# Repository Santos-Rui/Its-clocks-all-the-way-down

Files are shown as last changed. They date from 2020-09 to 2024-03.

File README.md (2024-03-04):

## Its clocks all the way down...

A digital clock made of 24 analog clocks.

Powered by an arduino, each clock handle is a stepper motor, totaling 48 steppers.

Why? because i'm part time masochist and like having to do the same thing dozens of times 

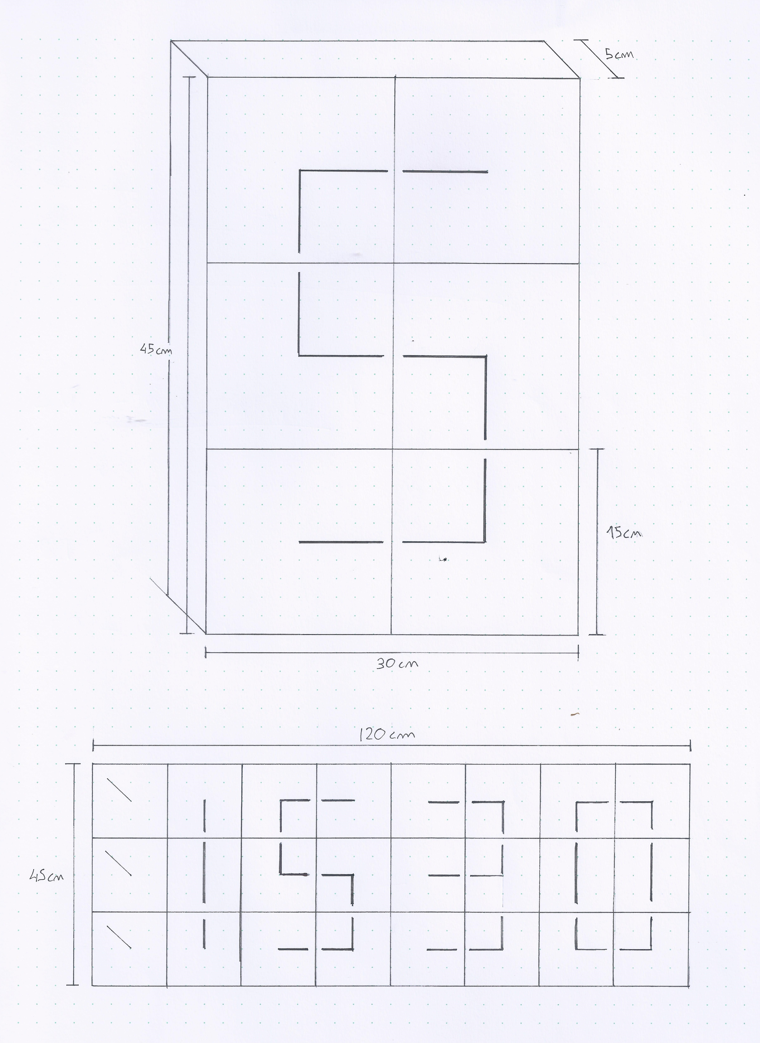
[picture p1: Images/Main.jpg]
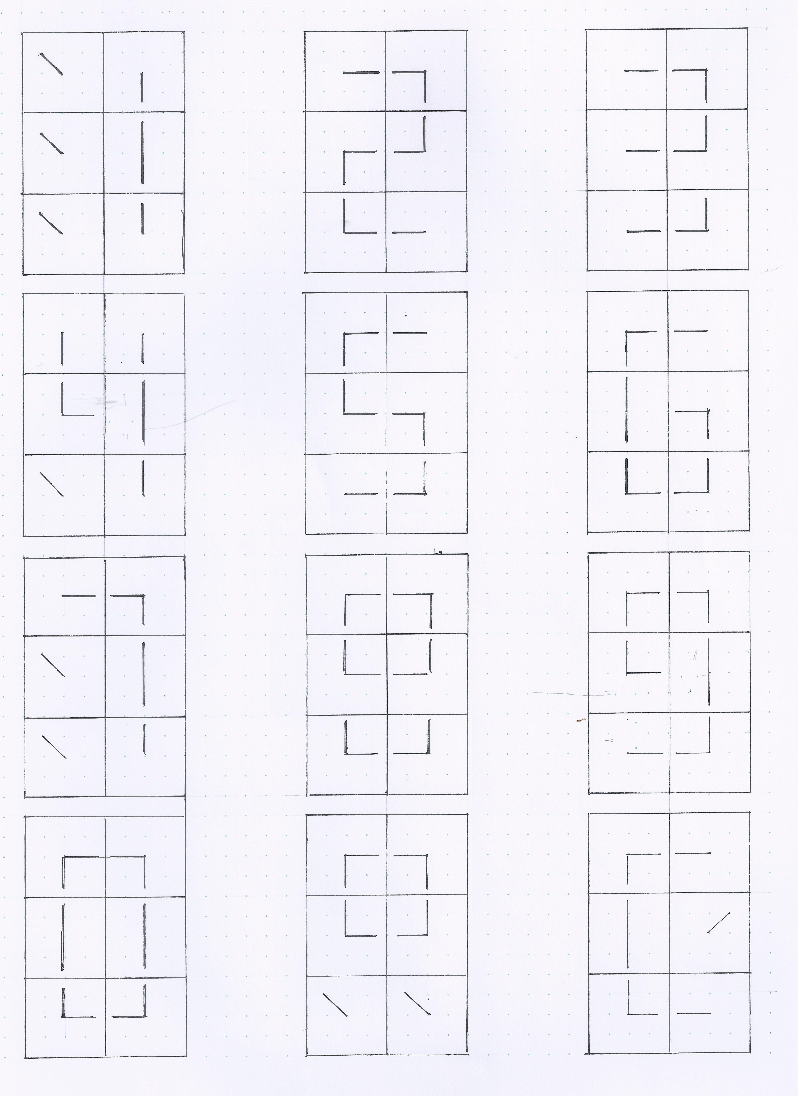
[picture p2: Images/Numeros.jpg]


[Click here for Video](https://www.youtube.com/watch?v=mT9d-I6LFRw)

~~The clock body, gears and handles will be laser cut (3 or 5mm) MDF, the handle shafts (shaft?) will be made with solid 8mm and 10mm alu with 1mm wall. All pieces (but the gears) will be designed from scratch in corel draw.~~

The clock "main body" will probably still be plywood/mdf. The body will now be only a front plate where the clock modules, psu, arduino and cables will atach (Maybe a back one for structure/tidiness). Later i can just do a thin pretty front cover and hide the screws. I will have to drill by hand though, the full clock wont fit the laser cutter.

The clock mechanism modules will now be fully 3d modeled printed, contaning ball bearings. Super gluing mdf to alu was already hard, keeping it all straight and square proved almost impossible and the end result was way too fragile. Modularity will allow me to swap/fix any clock without having to disassemble the whole thing. This will also probably help reducing slack and noise while increasing smootheness in the rotation

I'll also develop all the code (using some stepper libs) which will probably include some animations to make the transitions look nice, some kind of remote control, and maybe a small display for UI.

Also if you are still reading this, please help me design a better number 8.

## Version 1 
A simple, scaled down version using off the shelf gears. Only 1 clock for proof of concept
<details>
  <summary>Click to see more!</summary>
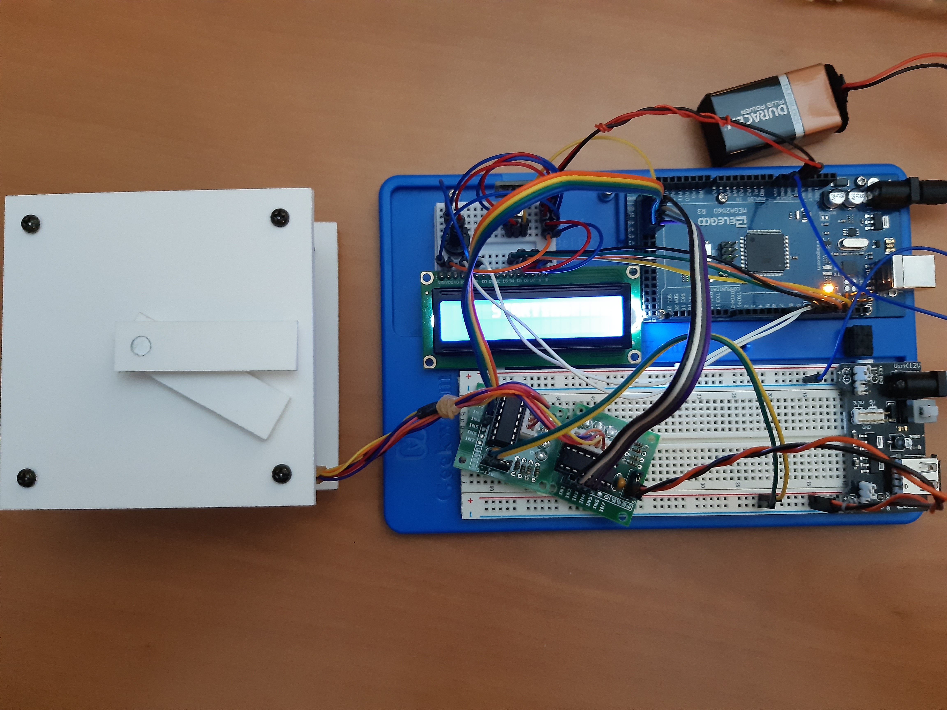
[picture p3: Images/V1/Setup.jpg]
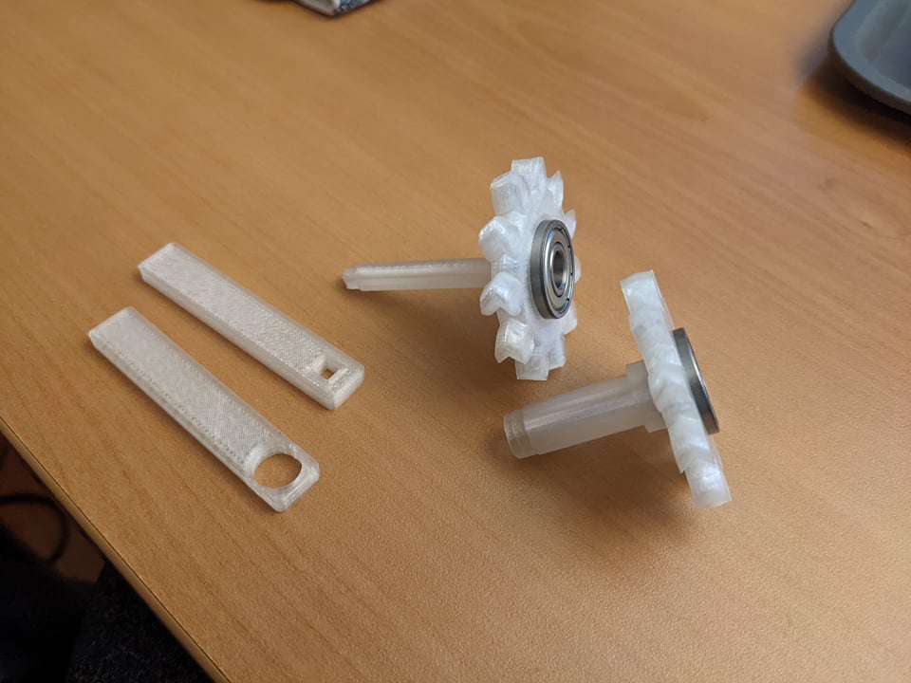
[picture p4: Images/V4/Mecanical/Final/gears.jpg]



</details>

## Version 2 
A full sized number (6 clocks, 12 motors). This will  already house the full size final power supply and the plan is to make it modular, so i can just add 3 more in the V3. Here ill need to implement some prettier control for the motors to move them in sync, and maybe some prettier transitions.
<details>
  <summary>Click to see more!</summary>

Fit test



Diagrams to laser cut

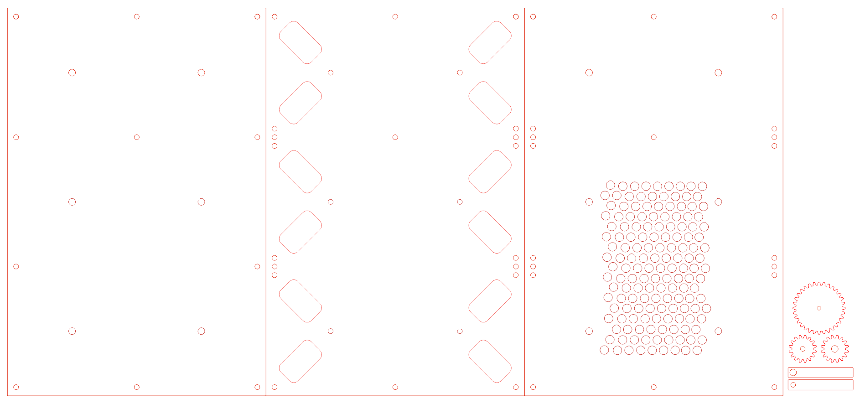
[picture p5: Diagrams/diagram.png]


First laser cutting try

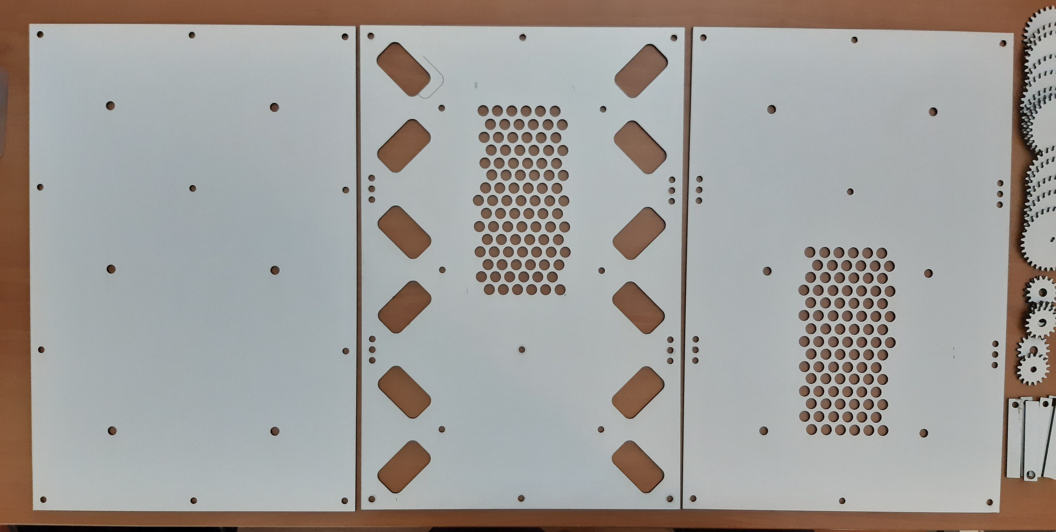
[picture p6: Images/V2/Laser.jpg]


Motors and corresponding gears installed. Also power supply and some power cable routing

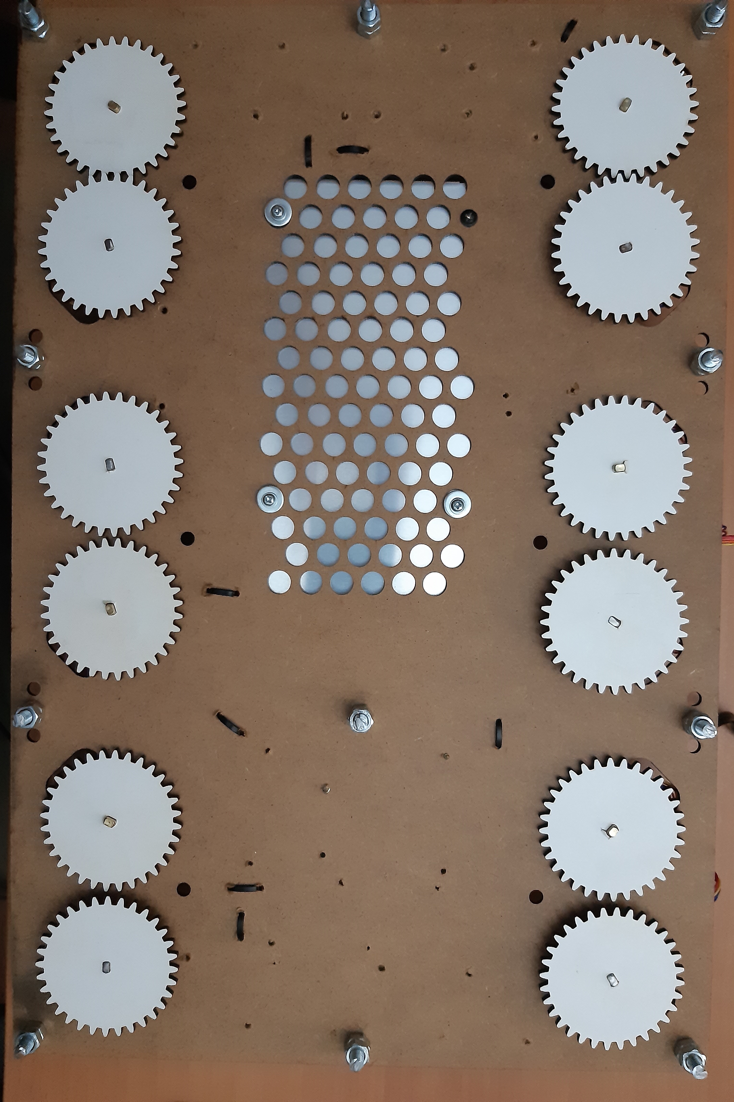
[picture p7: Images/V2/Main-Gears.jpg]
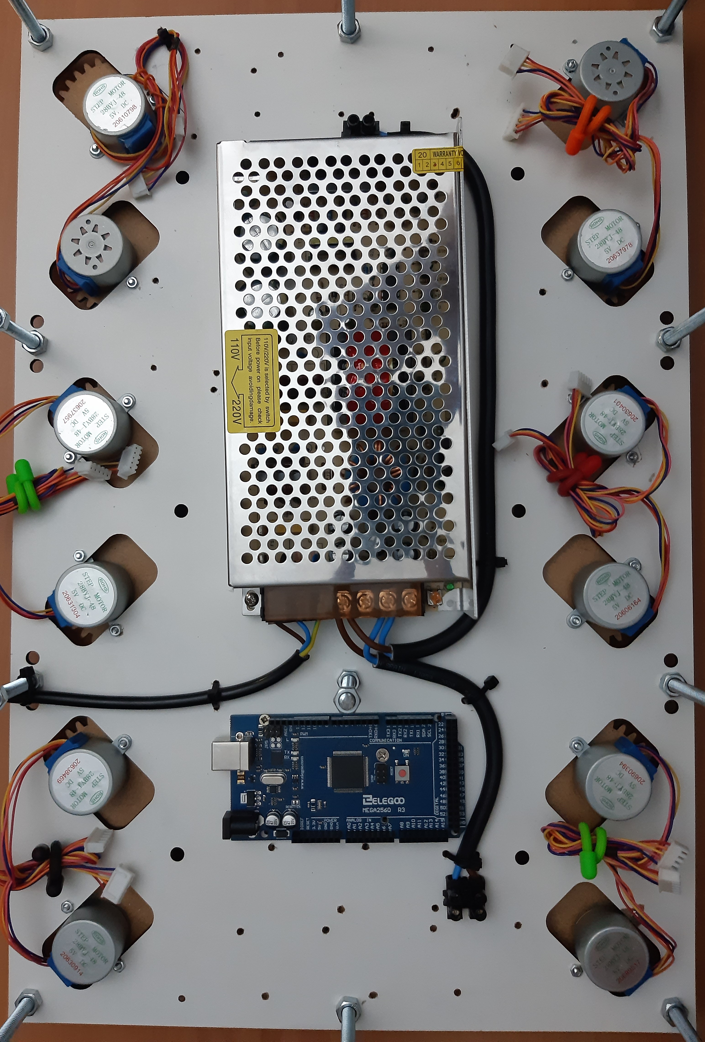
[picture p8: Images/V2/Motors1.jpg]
 

All driver boards installed, and motor cables routed.

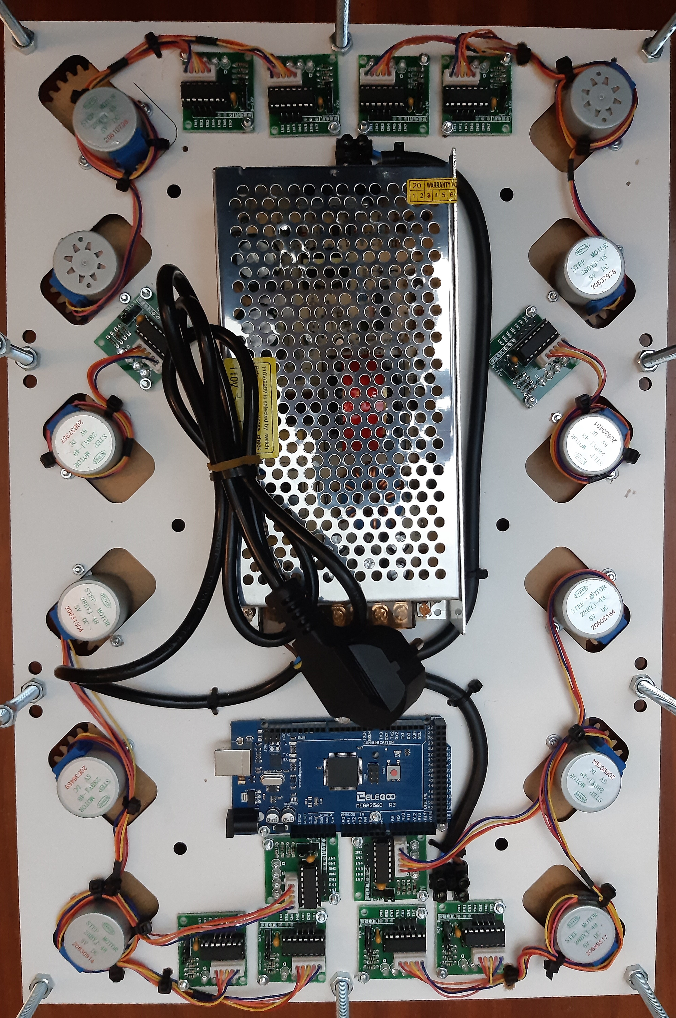
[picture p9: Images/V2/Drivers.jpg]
 

The plan was to solder every power and data cable, but soldering iron is shit and makes it way too hard, while the new one doesnt come, ill settle for custom cable lenght. Seems tidy enough

All power cables done

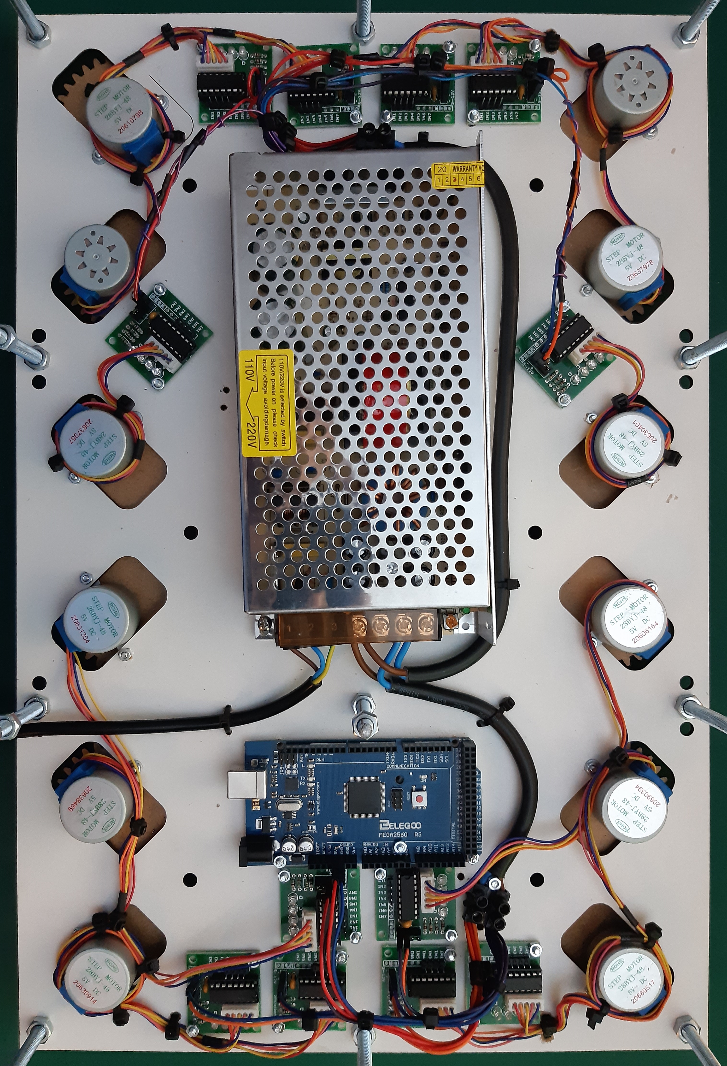
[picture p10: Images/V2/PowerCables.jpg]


At this point the soldering iron tip commited sudoku and melted itself, somehow. So for now ill have this spaghetti bundle of data cables to match the code i'll write for it after. After fixing a bunch of faulty cables, everything seems to be working on both eletrical and mechanical side.

 

The only problem is related to the gears. At this point the clock handles have somewhere between 5 and 10 degrees of play, not even close to acceptable. I ended up drilling the mottor mounts by hand, which led to some clearance between the cogs, added to the 2:1 ratio that doubled the ammount of error. I will need another iteration before going for the full clock only to handle the mechanical part.

### Coding

At this point i can start with the coding. The obvious problem is that moving a motor is a blocking function, so to move many motors simultaneously i will need to move all of them in tiny increments at a very fast pace. The AccelStepper library handles this already(to a degree), but i'm going to try an implementation from scracth. Ill compare it against AccelStepper later and see which fits better.
</details>

## Version 3 
A second iteraion with only number display, the backlash in the gearing was way to high, making it unusable.

<details>
  <summary>Click to see more!</summary>
The code was kinda working, but i need better base to actually test it. Ill redo V2 with a new mid-plate, and try to sodder everything, instead of connecting. 

Made some mockups to test the tolerance. Computer modeling can only take me so far, the laser cut, even though only 0.2mm ends up adding up to a big error

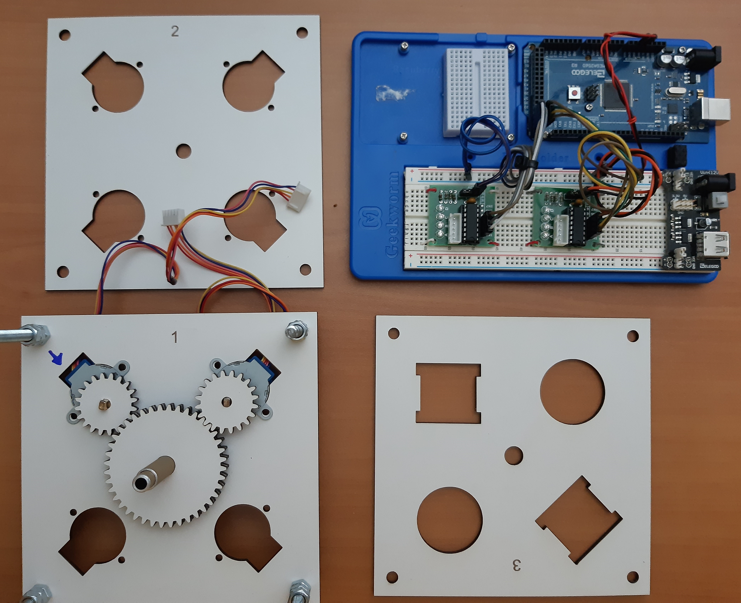
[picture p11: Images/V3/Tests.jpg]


And a new midplate is born

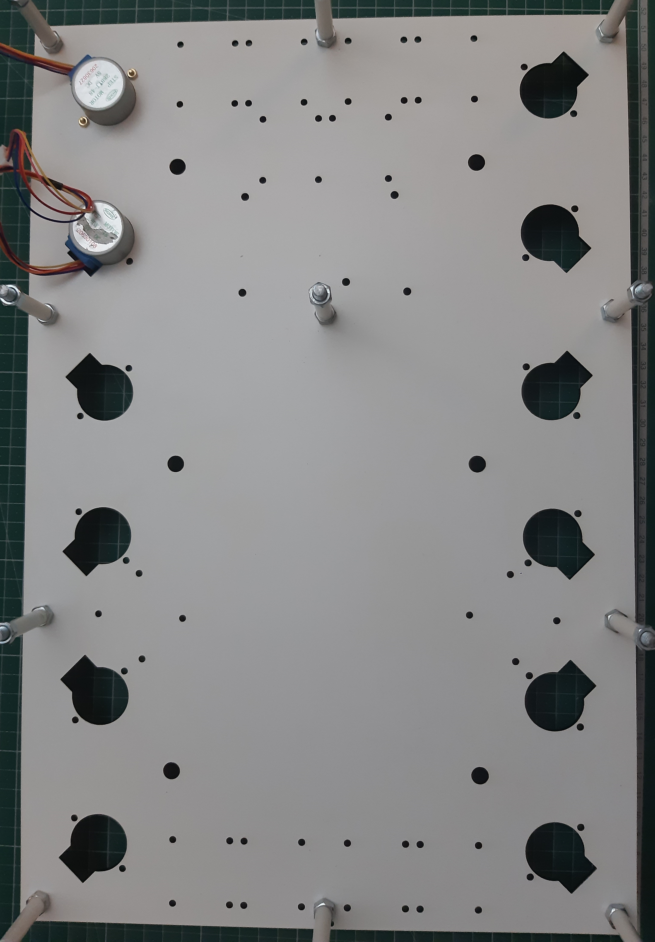
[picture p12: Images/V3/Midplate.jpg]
 

I could make it cleaner, but its good enough

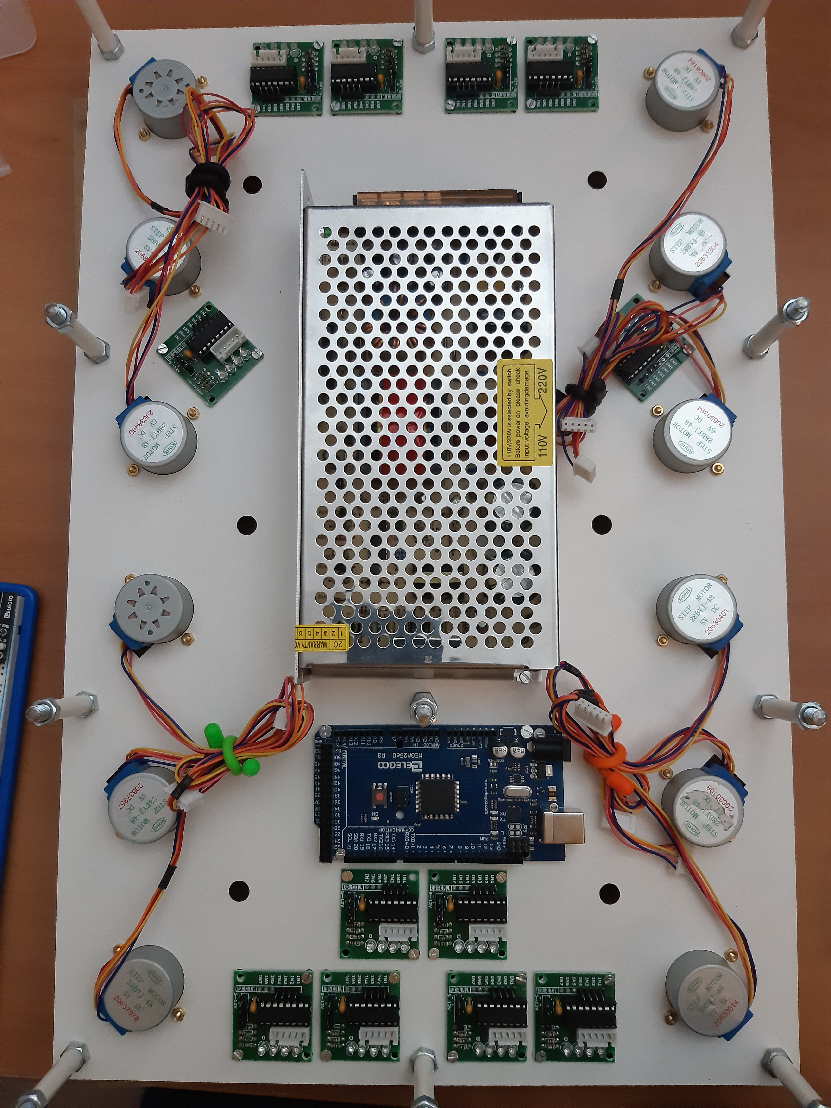
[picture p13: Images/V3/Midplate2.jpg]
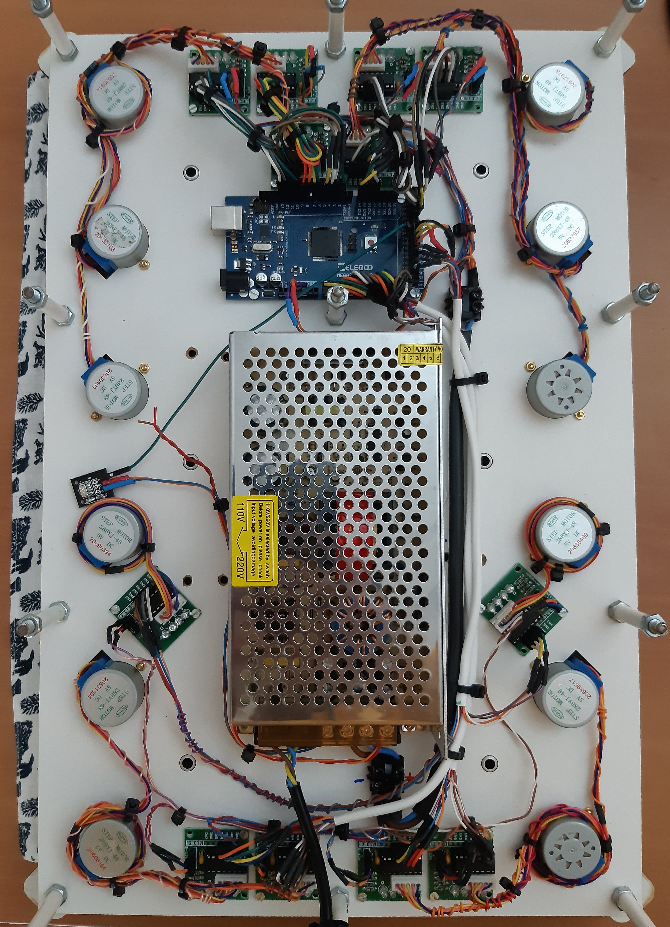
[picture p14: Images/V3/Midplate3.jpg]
 

On the mechanical side of things, gears are now running way smoother and with a fraction on the backlash.



A bit of code and some clock dials and we got
[Click here for Video](https://www.youtube.com/watch?v=mT9d-I6LFRw)
V3 Video (https://www.youtube.com/watch?v=mT9d-I6LFRw "V3 Video")

Im pretty happy with the results, not sure ill go any further, the repetitiveness  of the project is a bit overwhelming

</details>

## Version 4 
(Current) has 2 major differences. Modular clock mechanisms, 3d modedeled and printed. On the eletronics side i will need to expand the IO using shif registers or anything else that works really; the previous iteration had every stepper connected directly, which works but limits me at aprox 15 steppers.

<details>
  <summary>Click to see more!</summary>
  
  Prototyping
  
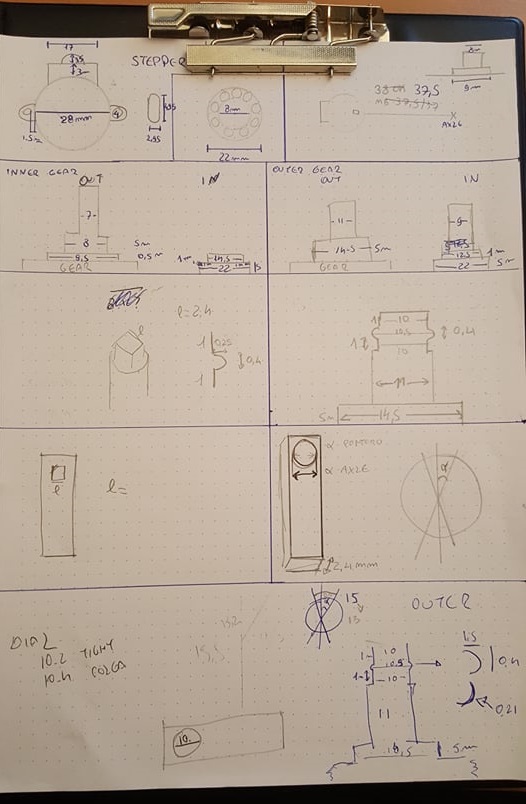
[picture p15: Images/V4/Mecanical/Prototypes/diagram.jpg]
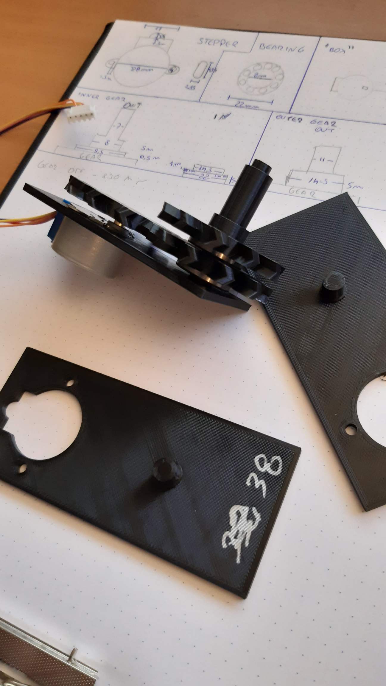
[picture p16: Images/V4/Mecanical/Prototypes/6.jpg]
     
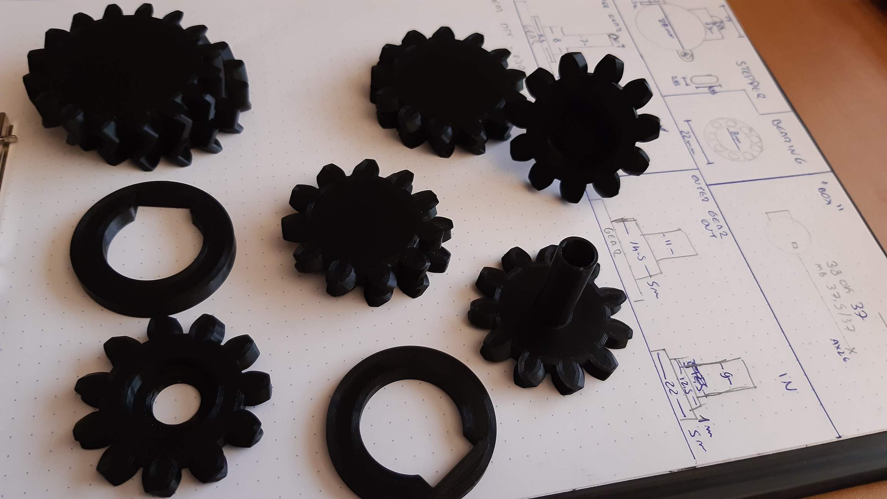
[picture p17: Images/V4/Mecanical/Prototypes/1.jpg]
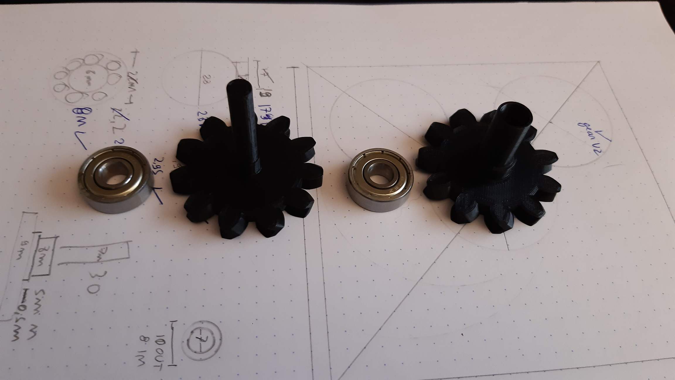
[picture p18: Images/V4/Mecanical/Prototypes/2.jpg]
            
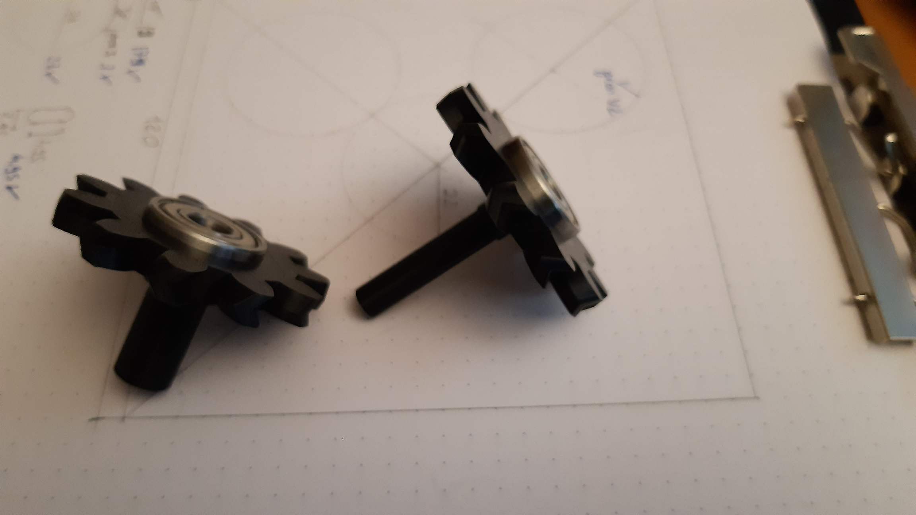
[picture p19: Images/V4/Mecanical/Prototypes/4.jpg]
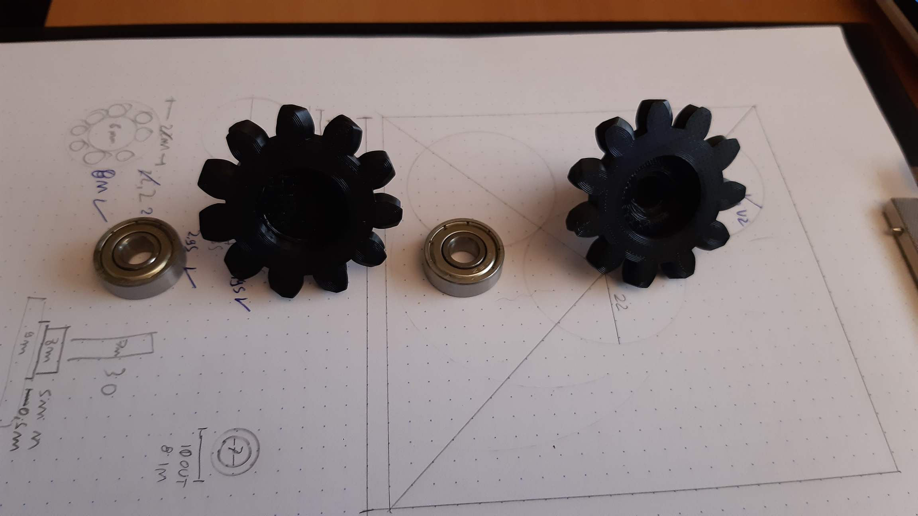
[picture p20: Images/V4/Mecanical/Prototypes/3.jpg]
      
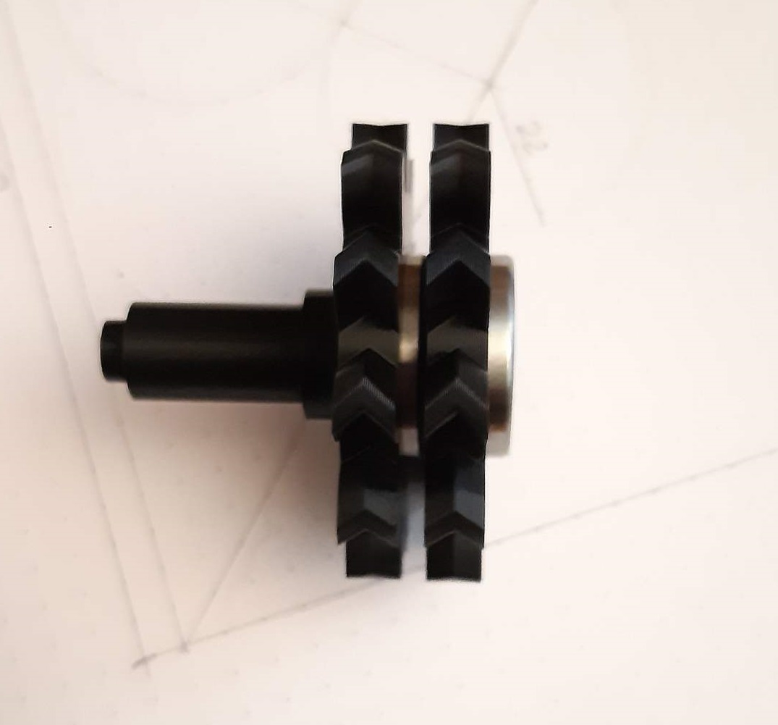
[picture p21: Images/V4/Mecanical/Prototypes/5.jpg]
  

  And the final mechanical version

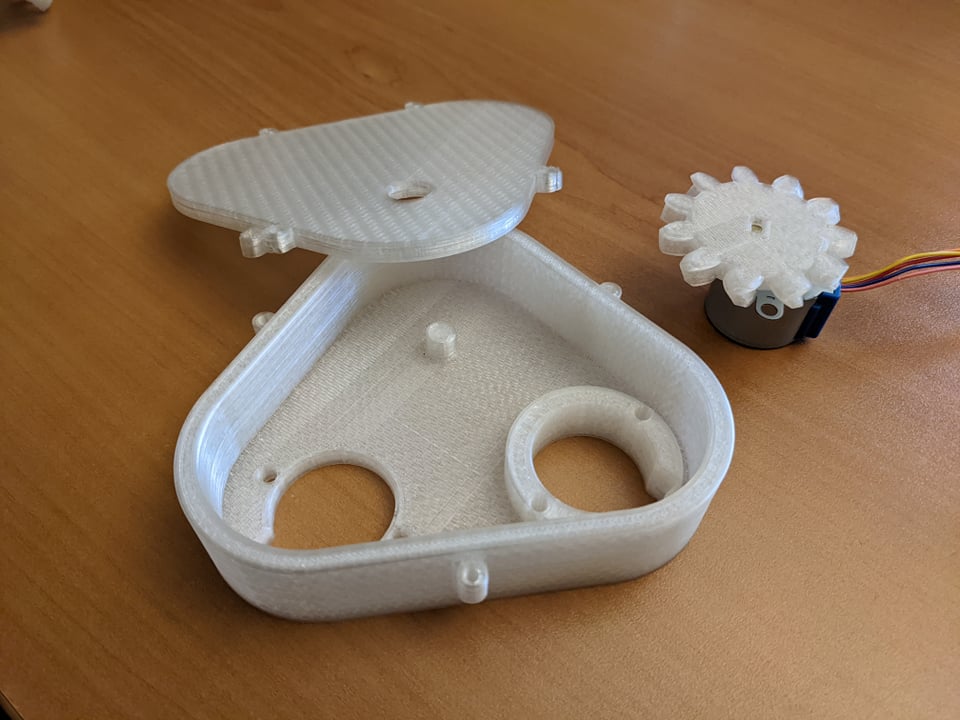
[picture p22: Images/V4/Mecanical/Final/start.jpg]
      
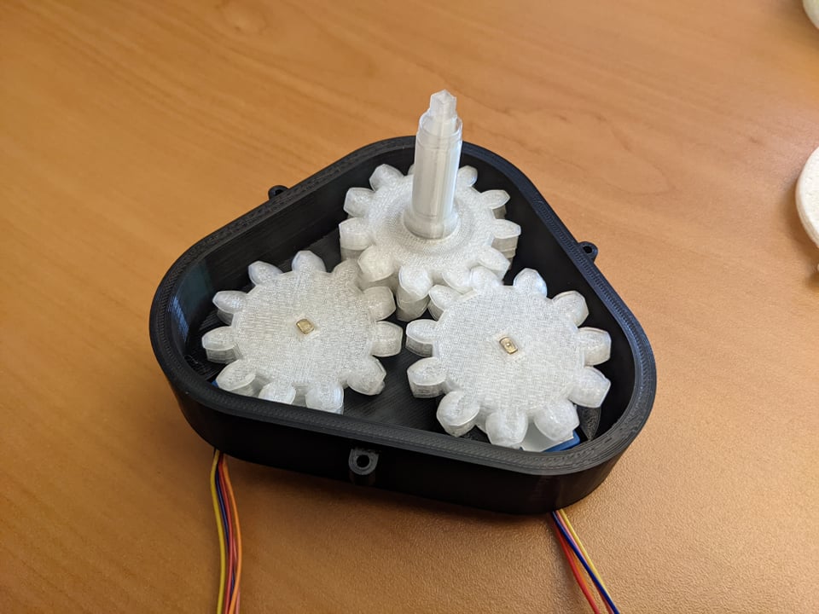
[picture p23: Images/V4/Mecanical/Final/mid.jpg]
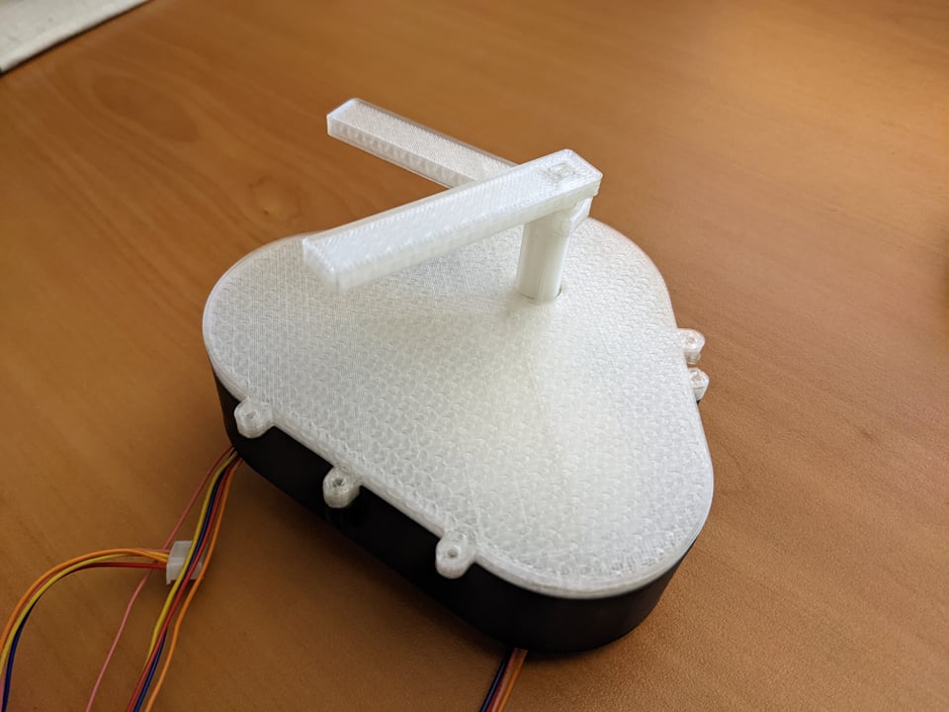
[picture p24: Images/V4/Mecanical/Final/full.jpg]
      

  The "final" version had some problems with slack. When using a bottom bearing to support both gears, meant the top one would have the combined play of both bearings. So i designed a finalfinal version, with a third bearing on top that couples to the lid, this way the gear assembly has almost zero lateral play.
  
     
          
     

  For the eletrical side of things, i pretty much given up on shift registers, so i'll most likely end up using one arduin for every digit, so 4 for the full clock.
  Comunication betwen arduinos seems easy, i might end up using a fifth arduino (a uno maybe) to calculate the positions of every dial, send them to the slaves and sync the start of movement.
  
  Since This time the plan is to actually build a clock and not a "digit", ill start by building the base board that will hold everything together. A 120x45cm board. Something like this
  
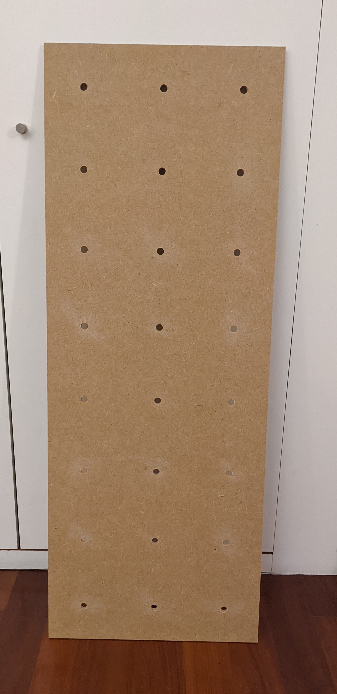
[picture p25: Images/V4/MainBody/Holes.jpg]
     
  
  Add a psu and some power cables
  
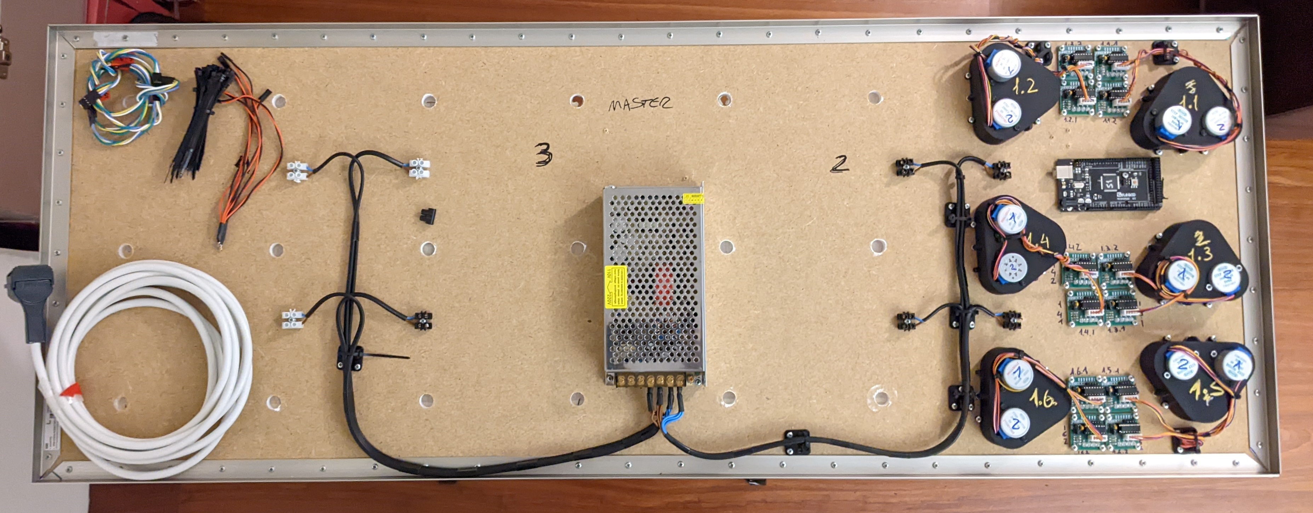
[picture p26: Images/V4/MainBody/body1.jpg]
     
  
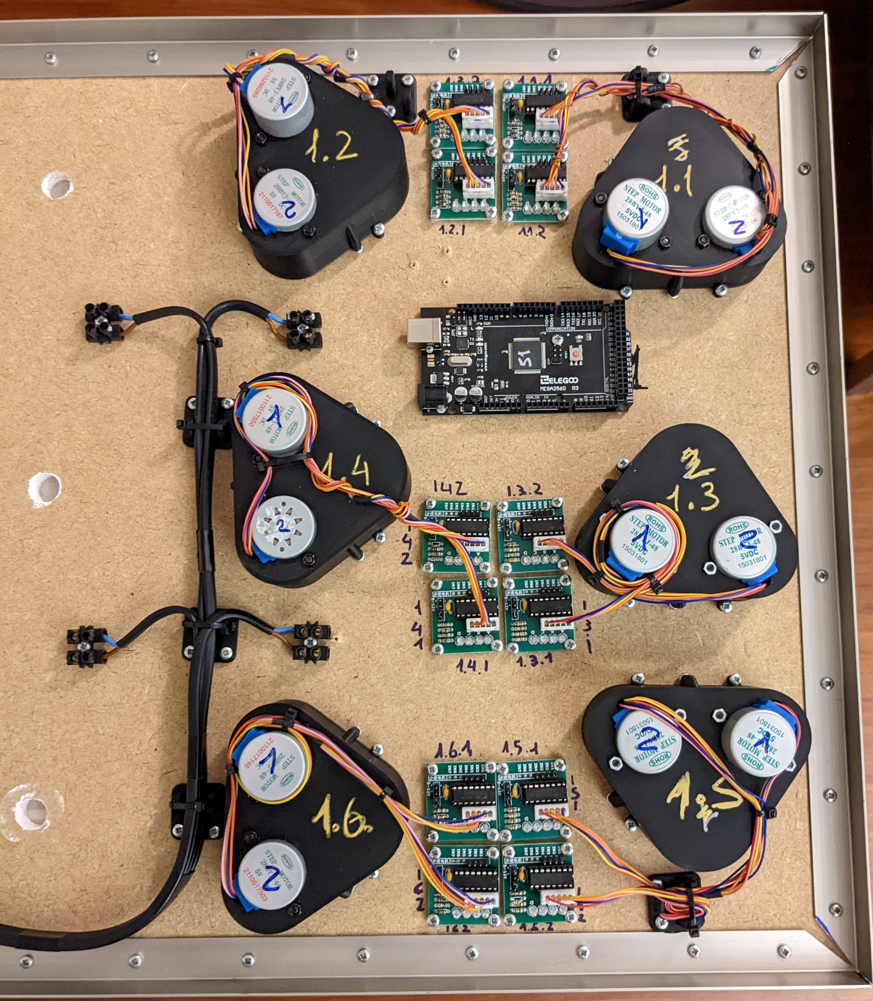
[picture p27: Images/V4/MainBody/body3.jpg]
  

  Some more data cables, and we have a functioning master slave/configuration. The slave is agnostic of any logic or numbers, it only receives positions, and some configs on how to move. After sending all the data, an aditional signal is sent to start moving every slave at once.
    
  
</details>

## Version N+1
This would be making it double, or 4 times as big so i could play with the animations and different number designs. Most likely will never exist.

## TO DO
<details>
  <summary>Click to expand!</summary>
  
Shift Registers - Expand IO - Nope

Using the same cable for 1-2 pin on every motor can theoretically give me 50% less IO ports needed. This will most likely NOT work - Nope

Turning every motor on and off on every step can also theoretically make me only need the current that one motor uses, and make it possible to wire them all in the same  circuit only using like 500mA , but can lead to drift overtime, will need testing. - Probably nope
</details>

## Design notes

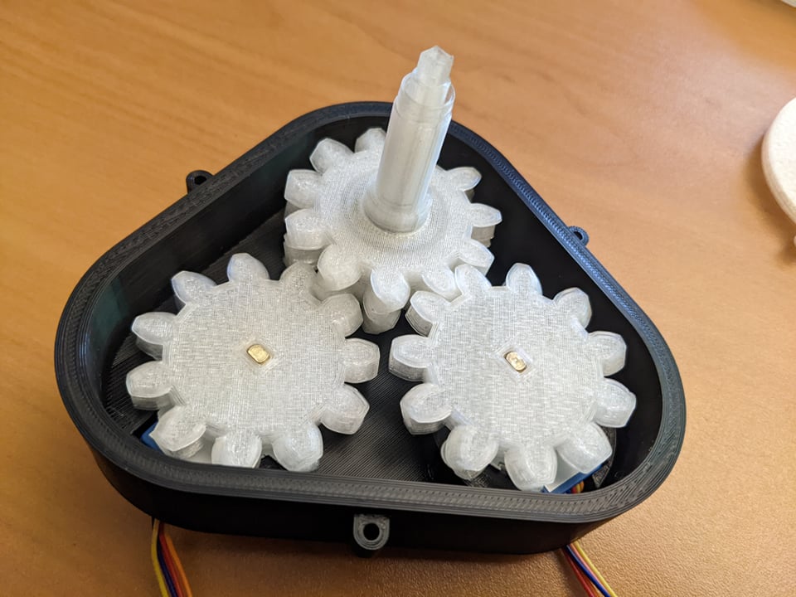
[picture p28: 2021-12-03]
Images/V4/Mecanical/Final/mid2.jpg

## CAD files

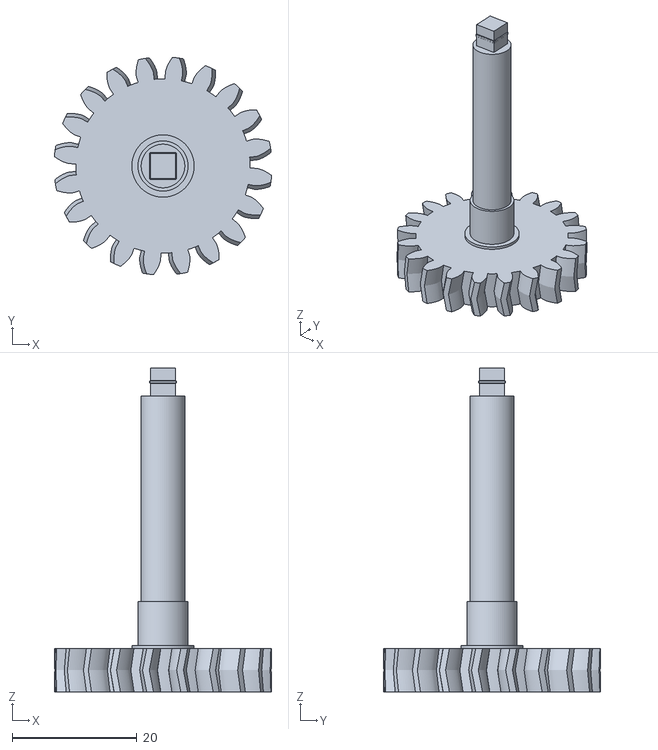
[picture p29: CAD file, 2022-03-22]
STL's/V2 Inner Gear v13.stl
34.9 x 34.9 x 52.0

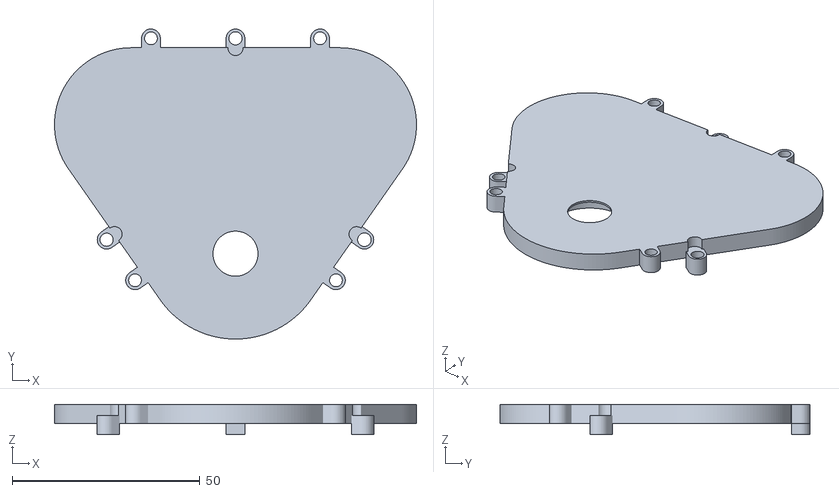
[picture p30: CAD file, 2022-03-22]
STL's/Cover.stl
96.5 x 82.6 x 8.00

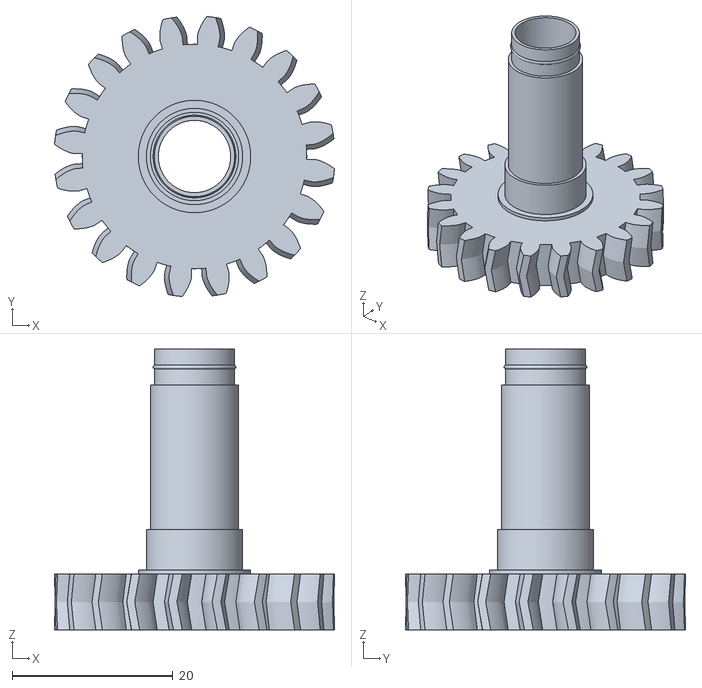
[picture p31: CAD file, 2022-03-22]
STL's/V2 Outer Gear v10.stl
34.9 x 34.9 x 35.0

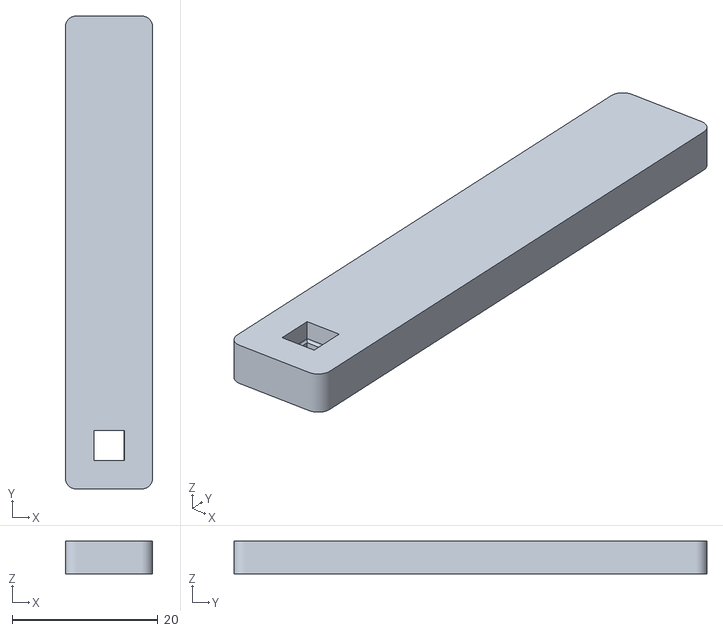
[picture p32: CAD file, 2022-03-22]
STL's/Dial in v4.stl
12.0 x 65.0 x 4.50

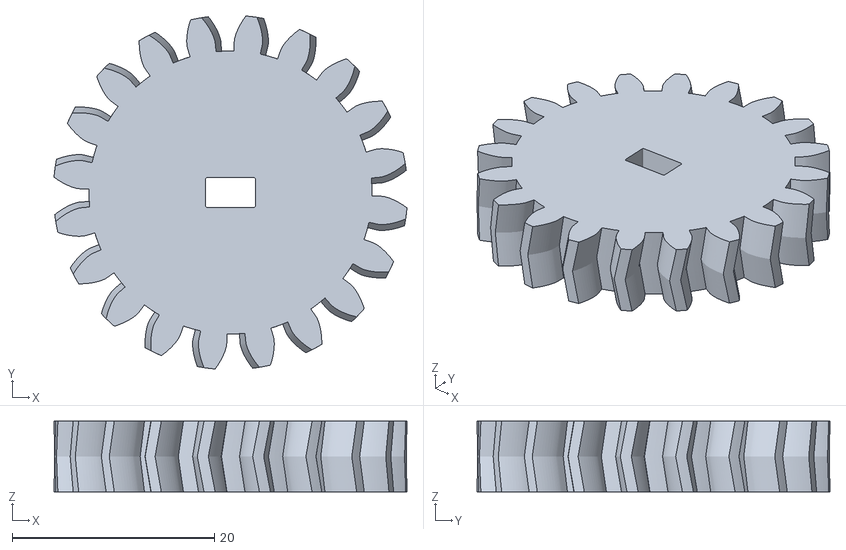
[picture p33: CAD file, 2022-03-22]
STL's/V2 Stepper Gear v9.stl
34.9 x 34.9 x 7.00

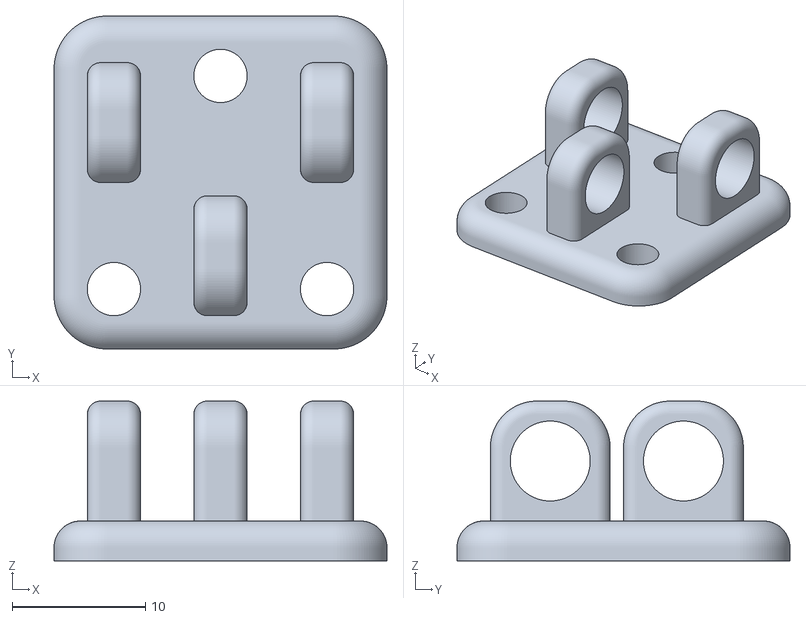
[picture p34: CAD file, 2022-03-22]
STL's/Cable tie clock v1.stl
25.0 x 25.0 x 12.0

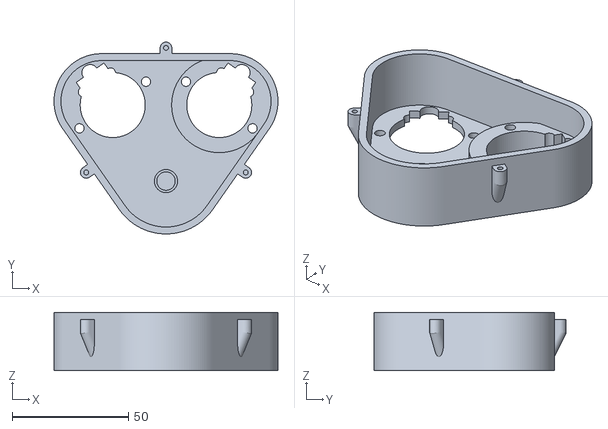
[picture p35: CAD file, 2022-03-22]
STL's/box.stl
96.5 x 82.6 x 25.0

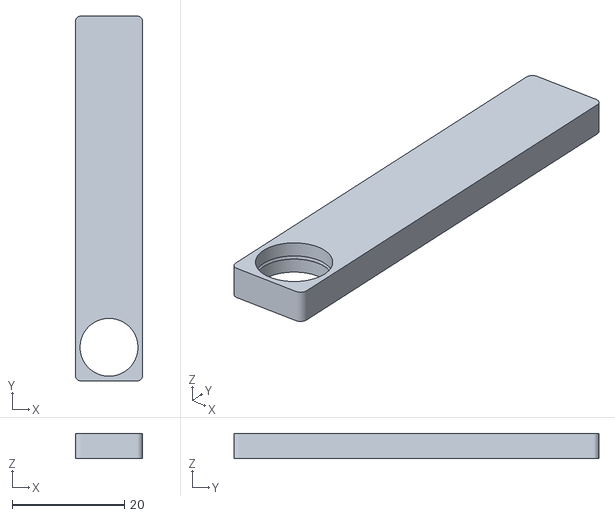
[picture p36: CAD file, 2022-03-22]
STL's/Dial out v2.stl
12.0 x 65.0 x 4.50

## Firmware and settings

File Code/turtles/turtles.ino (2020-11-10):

//  code for the V3 clock

#include <Stepper.h>
#include <IRremote.h>


const int stepsPerRev = 2048; // change this to fit the number of steps per revolution
const int lapFull = 4096;
const int qlap = 1024;

const int RPM = 15;           // Adjustable range of 28BYJ-48 stepper is 0~17 rpm
const int nrMotors = 12;

// IR
int RECV_PIN = 34;
IRrecv irrecv(RECV_PIN);
decode_results results;
unsigned long key_value = 0;
//IR

int rest[12]={0,0,0,0,0,0,0,0,0,0,0,0};
int zero[12]={1024,2048,2048,3072,0,2048,0,2048,0,1024,0,3072};
int um[12]={3584,3584,2048,2048,3584,3584,0,2048,3584,3584,0,0};
int dois[12] = {1024,1024,3072,2048,1024,2048,0,3072,0,1024,3072,3072};
int tres[12] ={1024,1024,3072,2048,1024,1024,3072,0,1024,1024,3072,0};
int quatro[12] ={2048,2048,2048,2048,0,1024,0,2048,3584,3584,0,0};
int cinco[12] ={1024,2048,3072,3072,0,1024,2048,3072,1024,1024,0,3072};
int seis[12] ={1024,2048,3072,3072,0,2048,2048,3072,0,1024,3072,0};
int sete[12] ={1024,1024,3072,2048,3584,3584,2048,0,3584,3584,0,0};
int oito[12] ={1024,2048,2048,3072,0,1024,0,3072,0,1024,0,3072};
int nove[12] ={1024,2048,2048,3072,0,1024,0,2048,1024,1024,0,3072};


typedef struct smotor {
  int currentPos = 0;
  int targetPos = 0;
  int lap = 0;
  int pins[4];
  Stepper * stepper;

  smotor(int a, int b, int c, int d){
      stepper = new Stepper(stepsPerRev, a , c , b , d);
      pins[0]=a;pins[1]=b;pins[2]=c;pins[3]=d;
      currentPos=targetPos=lap=0;
  }

  void setTarget(int target) {
      if(target<=currentPos){lap=1;}  //se tivermos a fretne temos de dar a volta
      
      targetPos = target;

  }

  void step() {

      if (currentPos==lapFull){
          currentPos=0;
          lap--;
      }
      if (lap > 0 || currentPos < targetPos){
          stepper->step(1);
          currentPos++;
      } 
//      Serial.println("Exiting step  lap =");
//      Serial.println(lap);
//      Serial.println("Cpos =");
//      Serial.println(currentPos);
//      Serial.println("Tpos =");
//      Serial.println(targetPos);
  }
}*motor;

//1 2 
//3 4
//5 6
motor listaMotors[nrMotors];

void createMotor() {
  listaMotors[0] = new struct smotor( 14  , 15 ,  16, 17 );  //1 top       
  listaMotors[1] = new struct smotor( 22 ,  24  ,26 , 28 );  //1 bottom   
  
  listaMotors[2] = new struct smotor( 2  ,  3  , 4  ,  5 );  //2 top         
  listaMotors[3] = new struct smotor( 6 ,   7  ,  8 ,  9 );  //2 bottom     
  
  listaMotors[4] = new struct smotor( 23 ,  25 , 27 , 29 );  //3 top       
  listaMotors[5] = new struct smotor( 38 ,  40  ,42 , 44 );  //3 bottom
  
  listaMotors[6] = new struct smotor( 10 ,  11 , 12 , 13 );  //4 top           
  listaMotors[7] = new struct smotor( 46 , 48  , 50 , 52 );  //4 bottom  
  
  listaMotors[8] = new struct smotor( A0,  A1 ,  A2,  A3 );  //5 top    
  listaMotors[9] = new struct smotor( A4,  A5 ,  A6 , A7 );  //5 bottom 
  
  listaMotors[10] = new struct smotor( A8,  A9 , A10, A11 );  //6 top        
  listaMotors[11] = new struct smotor( A12,  A13, A14, A15);  //6 bottom     
}


void motorSetup() {
  for (int i = 0; i < nrMotors; i++) {
    listaMotors[i]->stepper->setSpeed(RPM);
  }
}


void turnOffAll(){
  for (int i = 0; i < nrMotors; i++) {
        digitalWrite(listaMotors[i]->pins[0], LOW);
        digitalWrite(listaMotors[i]->pins[1], LOW);
        digitalWrite(listaMotors[i]->pins[2], LOW);
        digitalWrite(listaMotors[i]->pins[3], LOW);
    }
}


void moveAll(){


    for (int i = 0; i < nrMotors; i++) {
        listaMotors[i]->step();
    }
}

void draw(int lista[12]){
  for(int a=0;a<12;a++){
    listaMotors[a]->setTarget(lista[a]);
  }
}

void setup(){
    Serial.begin(9600);

    createMotor();
    motorSetup();
    irrecv.enableIRIn(); // Start  receiver

    delay(2000);
    Serial.println("exiting setup");
}


void loop() {
  if (irrecv.decode(&results)) {
  // if (results.value == 0XFFFFFFFF){
  //   results.value = key_value;
  // }

    switch(results.value){
        
      case 0xFF30CF:    // 1  
      case 0x9716BE3F: 
          draw(um); 
      break;

      case 0xFF18E7:   // 2
      case 0x3D9AE3F7:
          draw(dois); 
      break;

      case 0xFF7A85:   // 3
      case 0x6182021B:
          draw(tres); 
      break;

      case 0xFF10EF:   // 4
      case 0x8C22657B:
          draw(quatro); 
      break;

      case 0xFF38C7:   // 5
      case 0x488F3CBB:
        draw(cinco); 
      break;

      case 0xFF5AA5:   // 6
      case 0x449E79F:
         draw(seis); 
      break;

      case 0xFF42BD:   // 7
          draw(sete);
      break;

      case 0xFF4AB5:   // 8
      case 0xFF1BC01:
          draw(oito);
      break;

      case 0xFF52AD:   // 9
          draw(nove);
      break;

      case 0xFF6897:   // 0
          draw(zero);
      break;



      case 0xFFA25D:   // POWER
          draw(rest);
      break;


      default:
      break;
        }



       
      //Serial.println(results.value, HEX);
      key_value = results.value;
      irrecv.resume();// Receive the next value
  }

  moveAll();
  //delay(30000);
}

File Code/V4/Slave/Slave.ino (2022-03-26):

#include <Dto.h>
#include <CustomStepper.h>  
#include <Stepper.h>
#include <Wire.h>                               

//number of the slave
const int slaveNr = 1; //hours number 1 (left)

//pin to trigger movement
int triggerPin = 25;    

// RGB Pins
#define BLUE 29
#define GREEN 31
#define RED 33


//stepper settings
const int stepsPerRev = 2048; //steps per revolution
const int RPM = 15;           // Adjustable range of 28BYJ-48 stepper is 0~17 rpm
const int nrOfSteppers = 12;


//control vars
boolean listeningMode = true;
boolean waitingMode = true;
static int steppersDone = 0;


//"buffers"
int val = 0;      // variable to store the read value
String buffer = "";


//Stepper positions
int stepPos[nrOfSteppers][4] = {
      {22,24,26,28},  {2 ,3, 4 ,5 }       ,    {10,11,12,13} ,  {6, 7, 8, 9},     // 1.1-1.2      2.1-2.2      1 2 
      {A4,A5,A6,A7},{A12,A13,A14,A15}     ,    {A0,A1,A2,A3} , {A8,A9,A10,A11},   // 3.1-3.2      4.1-4.2      3 4
      {47,49,51,53} , {39,41,43,45}       ,    {38,40,42,44} ,  {46,48,50,52}     // 5.1-5.2      6.1-6.2      5 6
};


//main struct
CustomStepper * stepperList[nrOfSteppers];


//intializes steppers with pins and rpm
void intializeMotors() {
    for (int i = 0; i < nrOfSteppers; i++) {
        stepperList[i] = new CustomStepper(stepsPerRev,stepPos[i][0],stepPos[i][1],stepPos[i][2],stepPos[i][3]);
        stepperList[i]->setRPM(RPM);
    }   
}


//maps the received dto to the global struct
void mapDtoToStruct (Dto dto) {
    for (int i = 0; i < nrOfSteppers; i++) {
        stepperList[i]->setTarget(dto.getData(i), dto.getLap(), dto.getShortest(), dto.getDirection());
    }
  }


//handles i2c recevive event
//reads byte by byte and writes it to a string untill the last char '}'
void receiveEvent(int size){
    Serial.println("\nreceved event");
    int i=0;
    while(0<Wire.available()){    
        char c = Wire.read();
        if (c == '!'){
          waitingMode = false;
          return;
          }
        
        buffer = buffer + c;
        if(c=='}'){
            Serial.println("Full string");
            Serial.println(buffer);
            listeningMode = false;
            break;
        }
    }
}


void setup(){
    Serial.begin(9600);
    Serial.println("Starting Setup");
    pinMode(RED, OUTPUT); pinMode(GREEN, OUTPUT); pinMode(BLUE, OUTPUT);
    digitalWrite(RED, HIGH);digitalWrite(GREEN, HIGH);digitalWrite(BLUE, HIGH); //white
    //Join i2c as a slave                           
    Wire.begin(slaveNr);
            
    //register the receiver                        
    Wire.onReceive(receiveEvent);

    //Steppers
    intializeMotors();
    delay(3000);
    digitalWrite(RED, LOW);digitalWrite(GREEN, LOW);digitalWrite(BLUE, LOW); //OFF
    Serial.println("Exiting setup");
    
}


void loop() {
    Serial.println("Starting loop Iteration...");    
    Serial.println("Starting waiting for data...");
    digitalWrite(RED, LOW);digitalWrite(GREEN, LOW);digitalWrite(BLUE, HIGH); //BLUE
    while (listeningMode){
        delay(25);
    }
    digitalWrite(RED, HIGH);digitalWrite(GREEN, LOW);digitalWrite(BLUE, LOW); //red
    
    Serial.println("Received data, creating dto...");
    Dto dto;
    dto.setDto(buffer);
    
    Serial.println("Mapping dto...");
    mapDtoToStruct(dto);

    //Clear buffer
    buffer = "";

    //Wait for the trigger to actually start moving
      Serial.println("Starting waiting for trigger wire...");
      while(waitingMode) {
  //      val = digitalRead(triggerPin); // read the input pin
  //      Serial.print("val = "); Serial.println(val);
  //      if (val == HIGH) {
  //            int highs = 0;
  //            while (highs<100) {
  //                val = digitalRead(triggerPin); // read the input pin
  //                if (val == HIGH) {
  //                    highs++;
  //                }
  //                else {break;}
  //            }
  //            if(highs == 100){
  //                waitingMode = false;
  //            }
//
  //      }
        delay(20);
    }
    digitalWrite(RED, HIGH);digitalWrite(GREEN, LOW);digitalWrite(BLUE, HIGH); //purple
    //move untill every stepper is done
    Serial.println("Moving...");
    while (steppersDone != nrOfSteppers){
        for (int i = 0; i < nrOfSteppers; i++) {
            //Serial.print("moving stepper "); Serial.println(i);
            boolean lastStep = stepperList[i]->move();
            if(lastStep){
                steppersDone++;
                Serial.print("Sppers done "); Serial.println(steppersDone);
            }
        }
    }     
    val=0;
    steppersDone = 0;
    listeningMode = true;
    waitingMode = true;
    Serial.println("Ending Iteration...\n\n"); 
}

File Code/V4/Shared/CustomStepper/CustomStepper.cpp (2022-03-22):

#include <Stepper.h>
#include <CustomStepper.h>
#include <Arduino.h>


CustomStepper::CustomStepper(int steps, int a, int b, int c, int d){
    stepper =  new Stepper(steps, a, c, b, d);
    pins[0]=a;pins[2]=b;pins[1]=c;pins[3]=d; 
};


void CustomStepper::setTarget(int target, bool lap, bool shortest, int direction) {
    //Serial.print("SetTarget\n Input\ntarget: ");
    //Serial.println(target);
    //Serial.print("shortest:");
    //Serial.println(shortest);
    //Serial.print("directiont: ");
    //Serial.println(direction);
    //Serial.print("lap: ");
    //Serial.println(lap);
    //Serial.print("\n internal-\ntargetPos:");
    //Serial.println(targetPos);
    //Serial.print("currentPos: ");
    //Serial.println(currentPos);
    //Serial.println("\n");
  
    if (lap) {
        if((target<=currentPos && direction == 1) || (target>currentPos && direction == -1)){//se tivermos a fretne temos de dar a volta
            lap=1;
        }
    }

   if(target == currentPos && lap == 0) {
       //Serial.println("SamePos,lap+ anyway");
       this->lap=1;
   }

    if (shortest){
        //calculate shortest direction          //TODO
    }
    else {
      direction=direction;
    }

    targetPos=target;
    doneMoving=false; 
}


void CustomStepper::setRPM (int RPM) {
    stepper->setSpeed(RPM);
}


bool CustomStepper::move() {
    //Serial.print("current pos  "); Serial.println(currentPos);
    //Serial.print("targetPos pos  "); Serial.println(targetPos);
    if(doneMoving) {
        return false;
    }

    if  (currentPos == 2048){                            
        lap--;    
        currentPos = 0;                                  
    }
    if (currentPos != targetPos || lap > 0){        
        //stepper->step(1);
        currentPos++;
        return false;                            
    }

    if (currentPos == targetPos && lap == 0){
        Serial.println("Last Step...");              
        doneMoving = true;
        return true;
    }
   return false;

 // if(doneMoving) {
 //     //Serial.println("Done Moving...");
 //     return false;
 // }
 //
 // if (currentPos == lap && direction == 1 && lap>0){   //lap situation (when its at the top){
 //     Serial.println("Lap-- case 1...");
 //     lap--;    
 //     currentPos = 0;                                  //reset position
 // }
 // else if (currentPos == 0 && direction == -1){        //lap situation (when its at the top)
 //     Serial.println("Lap-- case 2...");                
 //     lap--;
 //     currentPos = lap;                                //reset position
 // }
 // if (currentPos != targetPos || lap > 0){             //if not already in target move one step
 //     //Serial.println("Move 1 step...");
 //     stepper->step(direction);
 //     currentPos+=direction;
 // }
 //
 //if (currentPos == targetPos && lap == 0){
 //     Serial.println("Last Step...");              
 //     doneMoving = true;
 //     return true;
 //}
   //delay(5000);
   //return false;         
}

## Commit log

2020-08-03 Inicial, so codigo mt simple para começar
2020-09-21 Motors and main gears + power suply and some cabling
2020-09-25 powercables + drivers
2020-10-01 first code prototype. Its working although pretty slow for some reason. Im sending tons of logs though, thats most likely it
2020-11-10 some weird sorcery is bugging this...
    [safe copy.cpp, turtles.ino]
2020-11-10 animations could use some work, but everything is working bug free!
    [safe copy.cpp, turtles.ino]
2022-02-19 V4 code, slave base, missing comunication
    [IR + LCD + Steppers.cpp, NoAccelStepper.cpp, Slave.ino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]
2022-03-22 fight the system, right a long but still useless commit
    [Cable tie clock v1.stl, Cover.stl, Dial in v4.stl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]
